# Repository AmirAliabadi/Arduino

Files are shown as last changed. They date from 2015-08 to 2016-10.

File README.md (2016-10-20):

# Arduino
Arduino related projects and libraries. 

quadcopter, dmp 6050, PID tuning

frame + esc + motor = 900g
each esc+motor+prop = 100g
large battery = 410g
small battery = 175g
flight controller = 50g

AUW with the wooden frame:
~1400g with large battery
~1200g with small battery

PID values that worked on the single boom:
Stable: 3.075, 0.0, 0.0
Rate: 0.475, 0.0, 0.004
Alpha: 0.92

Stable: 3.11, 0.0, 0.00
Rate: 0.515, 0.0, 0.08
Alpha: 0.80

-----
For the threaded brushless motors:
The direction you want the motor to spin is the direction that causes the nut to get tighter if you hold the nut still with your fingers.

ESC motor pairs
attach sync noise not in sync
001 paired with 001
xxx paired with 002

attach sync noise in sync 
001 paired with 003
xxx paired with 002

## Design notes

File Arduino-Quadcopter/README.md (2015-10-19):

Arduino-Quadcopter
=========

An arduino sketch for controlling a quadcopter. Uses RC and the MPU-6050 chip.

This is a simple arduino sketch that allows you to take over control over a quadcopter with the arduino board.
Because I've made this sketch primarily for private use, the sketch relies on certain hardware, but should also be
usable with different hardware with a bit of customization work.

This sketch was only tested on the Arduino Uno rev 3 board, so it might not work on other arduino-like boards without
making changes.

The arducopter sketch needs three things to work at the moment:

- A RC receiver with a minimum of 4 channels
- The MPU-6050 gyro/accelerometer chip
- Four ESCs with a known minimum and maximum value

At the moment, the sketch doesn't implement all features as I can only update it as fast as I can run new tests
with my quadcopter.
Complete features are:

- Arming of ESCs with given min/max values
- Control over pitch, roll and yaw through motor speed balances
- Control over pitch, roll and yaw through RC
- Controll over vertical speed through RC
- Calculation of current pitch, roll and yaw via the DMP unit on the MPU-6050

Planned features are:

- Automatic stabilisation of flight via MPU-6050 (complete but not fine tuned)
- Assisted safe landing through free fall detection

More features will be added as I expand the usage of my quadcopter.

In order to use this sketch, you will need to install the libraries from [arducopter/libraries](https://github.com/strangedev/arducopter/tree/master/libraries)
on your computer.

Note:
You cannot use the original Arduino-PID-Library wih this sketch. Please use the modified one included in this repo.

I want to thank [Jeff Rowberg](https://github.com/jrowberg), who created the great library [i2cdevlib](https://github.com/jrowberg/i2cdevlib) for using all
kinds of I2C devices including the MPU-6050 with the arduino board.
I also want to thank [br3ttb](https://github.com/br3ttb), who created the [Arduino-PID-Libary](https://github.com/br3ttb/Arduino-PID-Library/) which helped me save a lot of time.
Without their contributions to the open source community I couldn't have done this project.

Modifying the sketch
====================
***
*Note:* If you have questions about the code or the compatability of the code and certain hardware, you've spotted a bug or need help with your project, please open a new github issue rather than sending me an e-mail. That way, I don't have to answer questions twice and you'll get quicker answers. Thank you.
***
As I mentioned earlier, the sketch relies on certain hardware, but should work with all similar hardware aswell.
Fundemtal paramters of the used hardware, like the pin it's connected to, or minimum/maximum values of the ESCs are ``#define``'d
at the top of the sketch and can easily be changed to whatever value you prefer.

You might also want to change how the motor speed is affected by the signal coming in from the RC, for exmaple if your
copter is lighter or heavier than mine. At the moment this can only be done by changing the used equations in
``calculateVelocities()``.
However, I will improve my algorithms in the future and will probably find a way to easily fine tune the paramters of
the motor control.

Note:

The MPU-6050 board currently is the only supported gyro/accelerometer hardware and can only be connected in one specific 
way, due to the requirements of I2C and the fixed position of the Arduino's external interrupt pin.

License
=======

This project is licensed under the MIT license (see the included license file for more information).

Note: The libraries used in this project might not be licensed under the MIT license. I've made sure that the usage of all libraries as a part of this project, my modifications and the redistribution of the modified and unmodified libraries are permitted by the respective licenses, but the permissions of the MIT license might not apply, especially in regard to relicensing.

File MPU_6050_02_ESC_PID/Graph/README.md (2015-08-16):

#### Developed by Kristian Lauszus, TKJ Electronics 2012

The code is released under the GNU General Public License.
_________

This is the [Processing](http://processing.org/) application I made to visualize the data sent from the Arduino.

This should be used with the [MPU-6050](../) code I have provided.

Note that you properly need to change the serial port for it to work.

The serial port can be changed at the following line in the code:

```
serial = new Serial(this, Serial.list()[0], 115200);
```

For more information fell free to post a question at the guide: <http://arduino.cc/forum/index.php/topic,58048.0.html> or send me an email at <kristianl@tkjelectronics.dk>.

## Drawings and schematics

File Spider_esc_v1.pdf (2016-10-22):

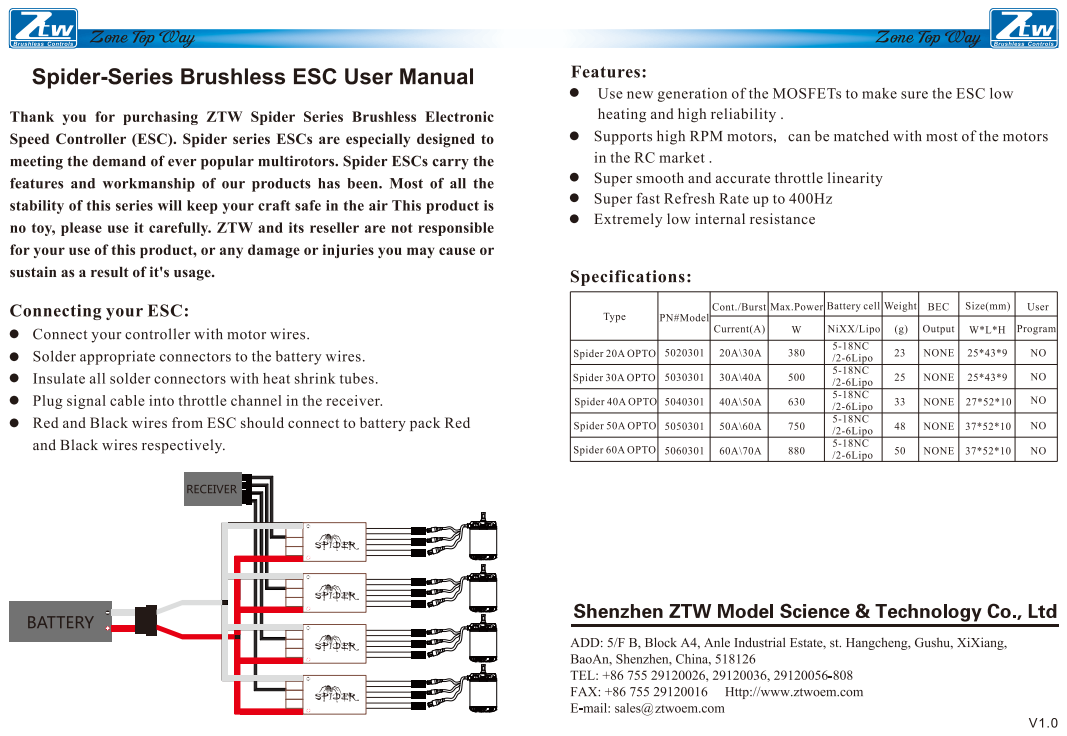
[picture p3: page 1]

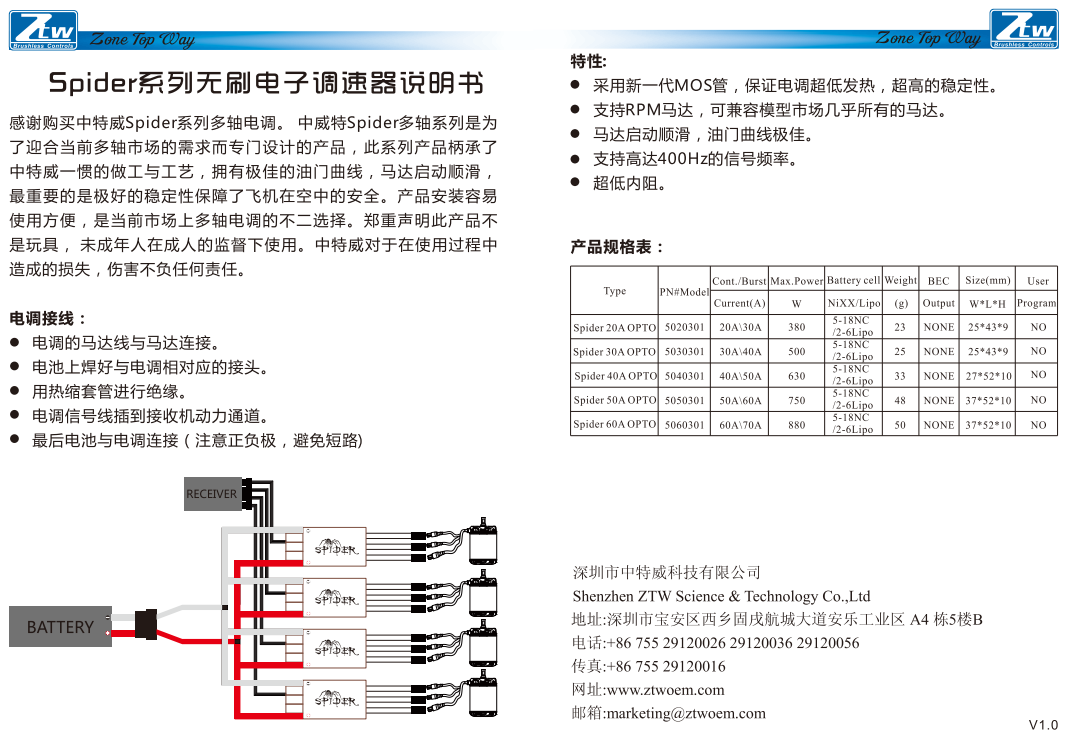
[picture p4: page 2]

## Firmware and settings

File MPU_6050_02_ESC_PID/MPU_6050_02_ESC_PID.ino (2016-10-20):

#include "Config.h"

//#include "MyServo.h"
//#define _ESC_ MyServo

#include "ESC.h"
#define _ESC_ ESC


#include <PID_v1.h>
#if I2CDEV_IMPLEMENTATION == I2CDEV_ARDUINO_WIRE
#include "Wire.h"
#endif
#include "I2Cdev.h"
#include "MPU6050_6Axis_MotionApps20.h"
//#include "MPU6050_9Axis_MotionApps41.h"
//#include "MPU6050.h" // not necessary if using MotionApps include file

byte update_pid_settings_needed = 1;
byte selected_pot_tuning = 0;
byte aserial_data_mode = 0;

float alpha = 0.88;
int pid_refresh_rate = 10;

#define DEBUG
//#define USE_INTERRUPTS
#define CASCADE_PIDS

/*
 * Single Boom PID values
 * ----------------------
 * 5.07, 0.00, 0.00
 * 0.443, 0.034, 0.112
 * 
 * 2.49, 0.00, 0.00       works but slugish
 * 0.376, 0.004, 0.004
 * 
 * alpha 0.02, pid rate 20
 * 2.615, 0.085, 0.065
 * 0.41, 0, 0.004
 * 
 * found some checkin notes about the d-term causing chatter
 *                           4.70,  0.0, 0.00,    // Stable P/I/D // .89,0,.23
 *                           1.20,  0.0, 0.16,    // Rate P/I/D
 *                           
 *  3.135, 0.0, 0.0
 *  0.672, 0.01, 0.013
 *  alpha 0.2, PID Refresh 5.0
 * 
 * *
 * Single Boom Quad PID
 * ---------------------
 * 6.885  0.00  0.405
 * 0.551  0.00  0.184
 * 
 * * 2.865 0.00 0.00
 * * 0.429 0.005 0.038
 */

///////////////////////////////////`
// user inputs
float input_values[17] = { 0,                       // thrust
                           3.135, 0.000, 0.000,     // Stable Pitch/Role PID P/I/D // .89, 0, .23
                           0.672, 0.010, 0.013,     // Rate Pitch/Role PID P/I/D
                           2.000, 0.000, 0.000,     // Stable Yaw 1.0, 0, 0.2,                 // YAW P/I/D
                           0.110, 0.000, 0.000,     // Stable Yaw 1.0, 0, 0.2,                 // YAW P/I/D
                           0.0, // setpoint yaw
                           0.0, // setpoint roll
                           0.0, // setpoint pitch
                           12.6                     // battery voltage level
                           };

// PID values:
// 4.7 / 0 / 0 | 1.2 / 0 / 0.16
// 2.681 / 0 / 0 | 0.967 / 0.125 / 0.096                           

#define INPUT_THRUST          input_values[0]

#define INPUT_STB_PID_P       input_values[1]
#define INPUT_STB_PID_I       input_values[2]
#define INPUT_STB_PID_D       input_values[3]

#define INPUT_RAT_PID_P       input_values[4]
#define INPUT_RAT_PID_I       input_values[5]
#define INPUT_RAT_PID_D       input_values[6]

#define INPUT_YAW_PID_P       input_values[7]
#define INPUT_YAW_PID_I       input_values[8]
#define INPUT_YAW_PID_D       input_values[9]

#define INPUT_YAW_RATE_PID_P       input_values[10]
#define INPUT_YAW_RATE_PID_I       input_values[11]
#define INPUT_YAW_RATE_PID_D       input_values[12]

#define INPUT_SETPOINT_YAW    input_values[13]
#define INPUT_SETPOINT_ROLL   input_values[14]
#define INPUT_SETPOINT_PITCH  input_values[15]
#define INPUT_VOLTAGE_LEVEL   input_values[16]

uint8_t setpoint_changed = SETPOINT_UNCHANGED;


float setpoint[3] = {0, 0, 0};
float last_setpoint[3] = {0, 0, 0};

//
//////////////////////////////////////////////////////////////////

//////////////////////////////////////////////////////////////////
// function pointer to what should be happing in the loop()
void (*process)(void);
void (*send_serial)(byte mode);
//
//////////////////////////////////////////////////////////////////

////////////////////////////////////////////////////////////////
// MPU setup
MPU6050 mpu;

// MPU control/status vars
bool dmpReady = false;  // set true if DMP init was successful
uint8_t mpuIntStatus;   // holds actual interrupt status byte from MPU
uint8_t devStatus;      // return status after each device operation (0 = success, !0 = error)
uint16_t packetSize;    // expected DMP packet size (default is 42 bytes)
uint16_t fifoCount;     // count of all bytes currently in FIFO
uint8_t fifoBuffer[64]; // FIFO storage buffer


// orientation/motion vars
Quaternion q;           			// [w, x, y, z]         quaternion container
VectorInt16 aa;         			// [x, y, z]            accel sensor measurements
VectorInt16 aaReal;     			// [x, y, z]            gravity-free accel sensor measurements
VectorInt16 aaWorld;    			// [x, y, z]            world-frame accel sensor measurements
VectorFloat gravity;    			// [x, y, z]            gravity vector

#ifdef CASCADE_PIDS    
VectorInt16 gyro;
VectorInt16 gyro1;
#endif

float ypr[3]      = {0.0f, 0.0f, 0.0f};
float ypr_last[3] = {0.0f, 0.0f, 0.0f};
float yw_offset   = 0.0;
float ac_offset   = 0.0;
float bd_offset   = 0.0;
//
////////////////////////////////////////////////////////////////


////////////////////////////////////////////////////////////////
// ESC
_ESC_ esc_a;
_ESC_ esc_b;
_ESC_ esc_c;
_ESC_ esc_d;

uint16_t va = MIN_ESC_SIGNAL;
uint16_t vb = MIN_ESC_SIGNAL;
uint16_t vc = MIN_ESC_SIGNAL;
uint16_t vd = MIN_ESC_SIGNAL;

uint16_t v_ac = 0;
uint16_t v_bd = 0;
//
////////////////////////////////////////////////////////////////

////////////////////////////////////////////////////////////////
// PID settings
float input_ypr[3]    = {0.0f, 0.0f, 0.0f};
float output_ypr[3]   = {0.0f, 0.0f, 0.0f};
float input_gyro[3]   = {0.0f, 0.0f, 0.0f};
float output_rate[3]  = {0.0f, 0.0f, 0.0f};

// input / output /setpoint
PID pid_stable[3]  = {
  PID(&input_ypr[YW], &output_ypr[YW], &setpoint[YW], 0, 0, 0, DIRECT),
  PID(&input_ypr[BD], &output_ypr[BD], &setpoint[BD], 0, 0, 0, DIRECT), 
  PID(&input_ypr[AC], &output_ypr[AC], &setpoint[AC], 0, 0, 0, DIRECT)
};

#ifdef CASCADE_PIDS
PID pid_rate[3] = {
  PID(&input_gyro[YW], &output_rate[YW], &output_ypr[YW], 0, 0, 0, DIRECT),
  PID(&input_gyro[BD], &output_rate[BD], &output_ypr[BD], 0, 0, 0, DIRECT),
  PID(&input_gyro[AC], &output_rate[AC], &output_ypr[AC], 0, 0, 0, DIRECT)
};
#endif

//
////////////////////////////////////////////////////////////////

////////////////////////////////////////////////////////////////
// MISC items
uint16_t system_check = INIT_CLEARED;

#ifdef DEBUG
long log_line = 0;
long last_log = 0;
#endif
long last_blink = 0;

////////////////////////////////////////////////////////////////


//// ================================================================
//// ===               INTERRUPT DETECTION ROUTINE                ===
//// ================================================================
//
#ifdef USE_INTERRUPTS
volatile bool mpuInterrupt = false;     // indicates whether MPU interrupt pin has gone high
void dmpDataReady()
{
  mpuInterrupt = true;

//  read_mpu();
//  read_throttle();
//  read_setpoint();
//  read_battery_voltage();
//  update_pid_settings();
//  
//  process();  
}
#endif

//////////////////////////////////////////////////////////////////////
// setup
void setup()
{
#ifdef DEBUG
  Serial.begin(115200); 
  while (!Serial);
#endif

  // configure LED for output
  pinMode(LED_PIN, OUTPUT);
  
  disarm_esc();
  init_i2c();
  init_pid();
  init_mpu();

  process = &wait_for_stable_process; //check_if_stable_process; //arm_esc_process;

  send_serial = &SerialSend_A;
}
//////////////////////////////////////////////////////////////////////


// ================================================================
// ===                    MAIN PROGRAM LOOP                     ===
// ================================================================
void loop()
{
  if ( millis() - last_blink > (system_check & INIT_ESC_ARMED == INIT_ESC_ARMED ? (INPUT_THRUST == 0 ? BLINK_FREQUENCY : BLINK_FREQUENCY / 2) : BLINK_FREQUENCY / 16) )
  {
    last_blink = millis();

    digitalWrite(LED_PIN, !digitalRead(LED_PIN));
  }

  if (!dmpReady) return;

#ifdef USE_INTERRUPTS
  // wait for MPU interrupt or extra packet(s) available
  while (!mpuInterrupt) // && fifoCount < packetSize)
  {
    read_throttle();        if (mpuInterrupt) break;
    read_setpoint();        if (mpuInterrupt) break;
    read_battery_voltage(); if (mpuInterrupt) break;
    update_pid_settings();  if (mpuInterrupt) break;

    process();
  }  
#endif

  read_mpu();
  read_throttle();
  read_setpoint();
  read_battery_voltage();
  update_pid_settings();
  
  process();

}

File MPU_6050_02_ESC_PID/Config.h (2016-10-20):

#define LED_PIN 13            // (Arduino is 13, Teensy is 11, Teensy++ is 6)
#define LOG_FREQUENCY  50     // ms DEBUG Logging interval
#define BLINK_FREQUENCY 1000

#define INIT_CLEARED          0b00000000
#define INIT_ESC_ATTACHED     0b00000001
#define INIT_ESC_ARMED        0b00000010
#define INIT_THROTTLE_ACTIVE  0b00000100
#define INIT_MOTORS_ENABLED   0b00001000
#define INIT_MPU_ARMED        0b00010000
#define INIT_MPU_STABLE       0b00100000
#define INIT_PID_ON           0b01000000
#define INIT_THROTTLE_ZEROED  0b10000000


#define SETPOINT_UNCHANGED    0b000
#define SETPOINT_CHANGED_AC   0b001
#define SETPOINT_CHANGED_BD   0b010
#define SETPOINT_CHANGED_YW   0b100

#define MPU_3

#ifdef MPU_1
#define MPU6050_ACCEL_OFFSET_X 699
#define MPU6050_ACCEL_OFFSET_Y -669
#define MPU6050_ACCEL_OFFSET_Z 1301
#define MPU6050_GYRO_OFFSET_X  47
#define MPU6050_GYRO_OFFSET_Y  -16
#define MPU6050_GYRO_OFFSET_Z  -30
#endif

#ifdef MPU_2
#define MPU6050_ACCEL_OFFSET_X -6542
#define MPU6050_ACCEL_OFFSET_Y -1314
#define MPU6050_ACCEL_OFFSET_Z 840
#define MPU6050_GYRO_OFFSET_X  39
#define MPU6050_GYRO_OFFSET_Y  -49
#define MPU6050_GYRO_OFFSET_Z  15
#endif

#ifdef MPU_3
#define MPU6050_ACCEL_OFFSET_X -62
#define MPU6050_ACCEL_OFFSET_Y 366
#define MPU6050_ACCEL_OFFSET_Z 1416
#define MPU6050_GYRO_OFFSET_X  161
#define MPU6050_GYRO_OFFSET_Y  145
#define MPU6050_GYRO_OFFSET_Z  -19
#endif


// mpu1
// 699  -669  1301  47  -16 -30
// 757  -662  1301  47  -12 -30

// mpu2
// -6640  -1344  832   38    -52   16
// -6542  -1314  840   39    -49   15
// -6545  -1318  834   45    -48   14

// mpu3
// 46 365 1393  163 143 -19
// 47 364 1394  162 143 -20
// 40 376 1398  162 142 -19
// 41 377 1398  162 142 -19
/*
Sensor readings with offsets:  -3  -7  16380 0 0 1
Your offsets: -64 373 1417  161 145 -19

Sensor readings with offsets:  2 -1  16388 0 1 1
Your offsets: -62 366 1416  161 145 -19
*/


/*
 *             (y)
                A Pitch +
                |
        Roll -  |
     (x)D -----[Y]----- B Roll +
                |(z)
                !
                C Pitch -

                USBaz
*/
#define YW 0
#define YAW 0
#define BD 1
#define ROLL 1
#define AC 2
#define PITCH 2
////////////////////////////////////////////////////////////////

////////////////////////////////////////////////////////////////
// throttle
#define THROTTLE_PIN 0

////////////////////////////////////////////////////////////////
// PID Tunning with a POT
#define Kp_PIN 0
#define Ki_PIN 1
#define Kd_PIN 2

////////////////////////////////////////////////////////////////
// ESC Settings
#define ESC_ARM_DELAY     3000
#define MAX_ESC_SIGNAL    2000    // This is the max output that will be sent to ESC.
#define MIN_ESC_SIGNAL    1000    // Minimum ESC signal
#define MIN_ESC_CUTOFF    1200    // Minimum ESC signal to ARM less than or equal to this should turn off motor completely
#define MOTOR_PIN_A       3       // setup with 500hz PWM pins
#define MOTOR_PIN_B       9       
#define MOTOR_PIN_C       11       
#define MOTOR_PIN_D       10      
/*
 * pin pairs:
 * 3 - 11 : default PWM frequency: 490.20 Hz
 * 9 - 10 : default PWM frequency: 490.20 Hz
 * 5 - 6  : default PWM frequency: 976.56 Hz
 */

/*
 * 
If you use the default values set by the Arduino Diecimila's bootloader, these are your PWM frequencies:
Arduino Pins 5 and 6: 1kHz
Arduino Pins 9, 10, 11, and 3: 500Hz
 */

// THROTTLE SETTINGS
#define MAX_INPUT_THRUST  1000    // 
#define MIN_INPUT_THRUST  0       // 

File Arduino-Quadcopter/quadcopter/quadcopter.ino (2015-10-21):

#ifndef QUADARDU
#define QUADARDU

#include <Servo.h>
#include <Wire.h>
#include <I2Cdev.h>
#include <helper_3dmath.h>
#include <MPU6050_6Axis_MotionApps20.h>
#include <PID_v1.h>
#include <PinChangeInt.h>
#include <PinChangeIntConfig.h>

#define DEBUG
#define MPU6050_ACCEL_OFFSET_X -6640
#define MPU6050_ACCEL_OFFSET_Y -1344
#define MPU6050_ACCEL_OFFSET_Z 832
#define MPU6050_GYRO_OFFSET_X  38
#define MPU6050_GYRO_OFFSET_Y  -52
#define MPU6050_GYRO_OFFSET_Z  -16

// board1 :   722  -654   1305  48    -16   -32
// board2 : -6640  -1344  832   38    -52   16



/*  Arduino Pin configuration
 *
 */

#define ESC_A 9
#define ESC_B 5
#define ESC_C 6
#define ESC_D 10

#define RC_1 13
#define RC_2 12
#define RC_3 11
#define RC_4 10
#define RC_5 8
#define RC_PWR A0


/* ESC configuration
 *
 */

#define ESC_MIN 1100 //22
#define ESC_MAX 1800 //115
#define ESC_TAKEOFF_OFFSET 1140 //30
#define ESC_ARM_DELAY 5000

/* RC configuration
 *
 */

#define RC_HIGH_CH1 1000
#define RC_LOW_CH1 2000
#define RC_HIGH_CH2 1000
#define RC_LOW_CH2 2000
#define RC_HIGH_CH3 1000
#define RC_LOW_CH3 2000
#define RC_HIGH_CH4 1000
#define RC_LOW_CH4 2000
#define RC_HIGH_CH5 1000
#define RC_LOW_CH5 2000
#define RC_ROUNDING_BASE 50

/*  PID configuration
 *
 */

#define PITCH_P_VAL .01
#define PITCH_I_VAL 0
#define PITCH_D_VAL .001

#define ROLL_P_VAL .01
#define ROLL_I_VAL 0 //5
#define ROLL_D_VAL .001

#define YAW_P_VAL 0
#define YAW_I_VAL 0 //5
#define YAW_D_VAL 0


/* Flight parameters
 *
 */

#define PITCH_MIN -30
#define PITCH_MAX 30
#define ROLL_MIN -30
#define ROLL_MAX 30
#define YAW_MIN -180
#define YAW_MAX 180
#define PID_PITCH_INFLUENCE 20
#define PID_ROLL_INFLUENCE 20
#define PID_YAW_INFLUENCE 20


/*  MPU variables
 *
 */

MPU6050 mpu;                           // mpu interface object


uint8_t mpuIntStatus;                  // mpu statusbyte
uint8_t devStatus;                     // device status
uint16_t packetSize;                   // estimated packet size
uint16_t fifoCount;                    // fifo buffer size
uint8_t fifoBuffer[64];                // fifo buffer

Quaternion q;                          // quaternion for mpu output
VectorFloat gravity;                   // gravity vector for ypr
float yrp[3] = {0.0f, 0.0f, 0.0f};     // yaw pitch roll values
float yrpLast[3] = {0.0f, 0.0f, 0.0f};

volatile bool mpuInterrupt = false;    //interrupt flag

/* Interrupt lock
 *
 */

boolean interruptLock = false;

/*  RC variables
 *
 */

float ch1, ch2, ch3, ch4, ch5;         // RC channel inputs

unsigned long rcLastChange1 = micros();
unsigned long rcLastChange2 = micros();
unsigned long rcLastChange3 = micros();
unsigned long rcLastChange4 = micros();
unsigned long rcLastChange5 = micros();

/*  Motor controll variables
 *
 */

int velocity;                          // global velocity

float bal_ac, bal_bd;                 // motor balances can vary between -100 & 100
float bal_axes;                       // throttle balance between axes -100:ac , +100:bd

int va, vb, vc, vd;                    //velocities
int v_ac, v_bd;                        // velocity of axes

Servo a, b, c, d;

/*  PID variables
 *
 */

#define YAW  0
#define PITCH 2
#define ROLL 1

PID pitchReg(&yrp[PITCH], &bal_ac, &ch2, PITCH_P_VAL, PITCH_I_VAL, PITCH_D_VAL, REVERSE);
PID rollReg(&yrp[ROLL], &bal_bd, &ch1, ROLL_P_VAL, ROLL_I_VAL, ROLL_D_VAL, REVERSE);
PID yawReg(&yrp[YAW], &bal_axes, &ch4, YAW_P_VAL, YAW_I_VAL, YAW_D_VAL, DIRECT);


/*  Filter variables
 *
 */

float ch1Last, ch2Last, ch4Last, velocityLast;

/*  Setup function
 *
 */

long last_log = 0;

float yaw_offset, pitch_offset, roll_offset;

void setup() {
    a.detach();
    c.detach();
    b.detach();
    d.detach();

    delay(10);
  
#ifdef DEBUG                        // Device tests go here
  Serial.begin(115200);                 // Serial only necessary if in DEBUG mode
  Serial.flush();
#endif

  //initRC();                            // Self explaining
  initMPU();
  initESCs();
  initBalancing();
  initRegulators();

  /*
    for(int i=0; i < 500; i++ ) {
      getYPR();
      delay(5);
    }

    yaw_offset = yrp[0];
    pitch_offset = yrp[2];
    roll_offset = yrp[1]; */


}

/* loop function
 *
 */

 boolean is_stable = 0;
 float last_yaw = 333;

void loop() {

  while (!mpuInterrupt) { // && fifoCount < packetSize){

    /* Do nothing while MPU is not working
     * This should be a VERY short period
     */

  }

  getYPR();

  if( is_stable ) {
    computePID();
    calculateVelocities();
    updateMotors();
  } else {
    if (millis() - last_log > 2000)
    {
      Serial.print(yrp[0]); Serial.print(F("\t"));
      Serial.println(last_yaw);
      last_log = millis();
      if( yrp[0] == last_yaw )
      {
        is_stable = 1;
        yaw_offset = yrp[0];
      } 
      else 
      {
        last_yaw = yrp[0];
      }
    }
  }
}

/*  computePID function
 *
 *  formats data for use with PIDLib
 *  and computes PID output
 */

void computePID() {

  acquireLock();

  /*
  ch1 = floor(ch1/RC_ROUNDING_BASE)*RC_ROUNDING_BASE;
  ch2 = floor(ch2/RC_ROUNDING_BASE)*RC_ROUNDING_BASE;
  ch4 = floor(ch4/RC_ROUNDING_BASE)*RC_ROUNDING_BASE;

  ch2 = map(ch2, RC_LOW_CH2, RC_HIGH_CH2, PITCH_MIN, PITCH_MAX);
  ch1 = map(ch1, RC_LOW_CH1, RC_HIGH_CH1, ROLL_MIN, ROLL_MAX);
  ch4 = map(ch4, RC_LOW_CH4, RC_HIGH_CH4, YAW_MIN, YAW_MAX);

  if((ch2 < PITCH_MIN) || (ch2 > PITCH_MAX)) ch2 = ch2Last;
  if((ch1 < ROLL_MIN) || (ch1 > ROLL_MAX)) ch1 = ch1Last;
  if((ch4 < YAW_MIN) || (ch4 > YAW_MAX)) ch4 = ch4Last;

  ch1Last = ch1;
  ch2Last = ch2;
  ch4Last = ch4;
  */
  ch1Last = 0;
  ch2Last = 0;
  ch4Last = 0;

////
//
////

  pitchReg.Compute();
  rollReg.Compute();
  yawReg.Compute();

  releaseLock();

}

/*  getYPR function
 *
 *  gets data from MPU and
 *  computes pitch, roll, yaw on the MPU's DMP
 */

void getYPR() {

  mpuInterrupt = false;
  mpuIntStatus = mpu.getIntStatus();
  fifoCount = mpu.getFIFOCount();

  if ((mpuIntStatus & 0x10) || fifoCount >= 1024) {

    Serial.println(F("Fifo overflow!"));
    mpu.resetFIFO();

  } else if (mpuIntStatus & 0x02) {

    while (fifoCount < packetSize) fifoCount = mpu.getFIFOCount();

    mpu.getFIFOBytes(fifoBuffer, packetSize);

    fifoCount -= packetSize;

    mpu.dmpGetQuaternion(&q, fifoBuffer);
    mpu.dmpGetGravity(&gravity, &q);
    mpu.dmpGetYawPitchRoll(yrp, &q, &gravity);

    /////
    //
    yrp[0] = yrp[0] * 180 / M_PI;
    yrp[1] = yrp[1] * 180 / M_PI;
    yrp[2] = yrp[2] * 180 / M_PI;
    
    yrp[0] = (float)((int)(( (yrp[0] - yaw_offset) * 10.0) +.5))/10.0;
    yrp[1] = (float)((int)((yrp[1] * 10.0) +.5))/10.0;
    yrp[2] = (float)((int)((yrp[2] * 10.0) +.5))/10.0;    
    
    if (abs(yrp[0] - yrpLast[0]) > 30) yrp[0] = yrpLast[0];
    if (abs(yrp[1] - yrpLast[1]) > 30) yrp[1] = yrpLast[1];
    if (abs(yrp[2] - yrpLast[2]) > 30) yrp[2] = yrpLast[2];
    
    yrpLast[0] = yrp[0];
    yrpLast[1] = yrp[1];
    yrpLast[2] = yrp[2];
    //
    //////    

  }

}
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

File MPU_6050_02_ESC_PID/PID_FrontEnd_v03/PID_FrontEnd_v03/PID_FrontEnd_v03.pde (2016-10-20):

/********************************************************
 * Arduino PID Tuning Front-End,  Version 0.3
 * by Brett Beauregard
 * License: Creative-Commons Attribution Share-Alike
 * April 2011
 *
 * This application is designed to interface with an
 * arduino running the PID Library.  From this Control
 * Panel you can observe & adjust PID performance in 
 * real time
 *a
 * The ControlP5 library is required to run this sketch.
 * files and install instructions can be found at
 * http://www.sojamo.de/libraries/controlP5/
 * 
 ********************************************************/

import java.nio.ByteBuffer;
import processing.serial.*;
import controlP5.*;

float last_throttle_position = 0;

float kp=0,ki=0,kd=0,krp=0,kri=0,krd=0;
float cur_throttle ;
float alpha =0.0 ;
float pid_refresh_rate=10.0 ;

/***********************************************
 * User spcification section
 **********************************************/
int windowWidth = 1350;      // set the size of the 
int windowHeight = 690;     // form

float InScaleMin = -75;       // set the Y-Axis Min
float InScaleMax = 75;    // and Max for both
float OutScaleMin = -125;      // the top and 
float OutScaleMax = 125;    // bottom trends


int windowSpan = 2000;//0;//00;    // number of mS into the past you want to display
int refreshRate = 10;      // how often you want the graph to be reDrawn;

float displayFactor = 1; //display Time as Milliseconds
//float displayFactor = 1000; //display Time as Seconds
//float displayFactor = 60000; //display Time as Minutes

// if you'd like to output data to 
// a file, specify the path here
String outputFileName = ""; 

/***********************************************
 * end user spec
 **********************************************/

int nextRefresh;
int arrayLength = windowSpan / refreshRate+1;
int[][] InputData = new int[3][arrayLength];
int[][] OutputData = new int[5][arrayLength];

float inputTop = 25;
float inputHeight = (windowHeight-70)*2/3;
float outputTop = inputHeight+50;
float outputHeight = (windowHeight-70)*1/3;

float ioLeft = 210, ioWidth = windowWidth-ioLeft-50;
float ioRight = ioLeft+ioWidth;
float pointWidth= (ioWidth)/float(arrayLength-1);

int vertCount = 10;
int nPoints = 0;

boolean madeContact =false;
boolean justSent = true;

Serial myPort;

ControlP5 controlP5;
controlP5.Button DRButton, DRrButton;

RadioButton serial_data_mode; //, tuning_mode;

float Input_Thrust, Input_Setpoint, Input_gyro, Input_angle, Output_angle, Output_gyro ;
byte i_serial_data_mode; 
float va,vb,vc,vd;
float pterm_stable, iterm_stable, dterm_stable;
float pterm_rate, iterm_rate, dterm_rate;

controlP5.Textlabel InputThrustLabel, InputSetpointLabel, InputGyroLabel, InputAngleLabel, AngleOutLabel, GyroOutLabel, AlphaLable, PidRefreshIntervalLabel;
controlP5.Textlabel PTermRateLabel, ITermRateLabel, DTermRateLabel;
controlP5.Textlabel PLabel, ILabel, DLabel, DRLabel, DRCurrent, DRrLabel, DRrCurrent, PrLabel, IrLabel, DrLabel ;

controlP5.Textlabel SPField; 

controlP5.Slider throttle_slider;

PrintWriter output;
PFont AxisFont, TitleFont; 

void setup()
{
  int group_x =0;
  int group_y =0;
  
  frameRate(30); // 30
  size(1350 , 690);

  println(Serial.list());   // * Initialize Serial
  
  if( Serial.list().length > 0 ) {
    myPort = new Serial(this, Serial.list()[0], 115200);                //   Communication with
    myPort.bufferUntil(10);         //   the Arduino
  }
  
  controlP5 = new ControlP5(this);                                    // * Initialize the various
  
  group_x = 80; group_y=140;
  
  controlP5.addTextlabel("t-1","Setpoint",group_x-80,group_y);  
  SPField= controlP5.addTextlabel("Setpoint","", group_x, group_y);
  
  controlP5.addTextlabel("t1","Throttle",group_x-80,group_y+=15);
  InputThrustLabel=controlP5.addTextlabel("InputThrustLabel","", group_x, group_y);
  
  controlP5.addTextlabel("t2","Setpoint",group_x-80,group_y+=15);
  InputSetpointLabel=controlP5.addTextlabel("InputSetpointLabel","",group_x,group_y);

  controlP5.addTextlabel("t4","Input Angle",group_x-80,group_y+=15);
  InputAngleLabel=controlP5.addTextlabel("InputAngleLabel","",group_x,group_y); 
  controlP5.addTextlabel("t3","Input Gyro",group_x-80,group_y+=15);
  InputGyroLabel=controlP5.addTextlabel("InputGyroLabel","",group_x,group_y);

  controlP5.addTextlabel("t5","Out Angle",group_x-80,group_y+=15);
  AngleOutLabel=controlP5.addTextlabel("AngleOutLabel","",group_x,group_y); 
  controlP5.addTextlabel("t6","Out Gyro",group_x-80,group_y+=15);
  GyroOutLabel=controlP5.addTextlabel("GyroOutLabel","",group_x,group_y);

  controlP5.addTextlabel("t7","Alpha",group_x-80,group_y+=15);
  AlphaLable=controlP5.addTextlabel("AlphaLable","",group_x,group_y);

  controlP5.addTextlabel("t71","PID Refresh",group_x-80,group_y+=15);
  PidRefreshIntervalLabel=controlP5.addTextlabel("PidRefreshIntervalLabel","",group_x,group_y);
  
  controlP5.addTextlabel("t72","PTerm Rate",group_x-80,group_y+=15);
  PTermRateLabel=controlP5.addTextlabel("PTermRateLabel","10",group_x,group_y);
  controlP5.addTextlabel("t73","ITerm Rate",group_x-80,group_y+=15);
  ITermRateLabel=controlP5.addTextlabel("ITermRateLabel","10",group_x,group_y);
  controlP5.addTextlabel("t74","DTerm Rate",group_x-80,group_y+=15);
  DTermRateLabel=controlP5.addTextlabel("DTermRateLabel","10",group_x,group_y);
  
  controlP5.addTextlabel("t8","Stable",group_x-80,group_y+=35);  
  controlP5.addTextlabel("t81","Rate",group_x,group_y);    
  
  controlP5.addTextlabel("t9","P: ",group_x-80,group_y+=15);    
  PLabel=controlP5.addTextlabel("Ps","0.00",group_x-70,group_y);                    //
  PrLabel=controlP5.addTextlabel("Pr","0.00",group_x,group_y);                    //
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

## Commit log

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2015-08-19 updated handle noise from the 6050 and updated to log the PID terms that are in effect. The serial out can easily be graphed in google charts.
    [MPU_6050_02_ESC_PID.ino]
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2015-09-07 more updates related to tuning pid, updated to use serialEvent() to read inputs from serial.
2015-09-11 more updates, working on eliminating vibrations from motors.
    [Logging.ino, MPU_6050_02_ESC_PID.ino]
2015-09-14 more PID tuning. A found out why MPU reading were bogus after a certain period of time.
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2015-09-17 finally good PID tuning values. The trick was to increate the PID compute frequency. The defualt of once every 100ms the PID_v1 has was to slow.
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2015-09-18 more PID tuning. I have found some PID values that seem to work.
2015-09-19 tested out the spyder ESC and they didn't perform as well as the yellow no-name amazone ESC i have been used. need to look into it more. Also, experimenting with reseting the PID when the setpiont ch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
    [Config.h, ESC.ino, ESC_Arming_with_POT.ino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]
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2015-09-25 bug fixes related to switching to bitmasks. Added the adaptive pid tuning and the concept of PD controller when far from setpoint and PID controller when close to setpoint
    [Config.h, ESC.ino, Logging.ino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]
2015-09-26 added the yaw and have started to get ready for the second boom to be in place.
2015-09-27 still working out the pid tunings and the adaptive pid values. found out that the quad stand was binding make it appear as if things were more stable than they actually were.
    [ESC.ino, I2C.ino, Inputs.ino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]
2015-09-30 removed teh fifoCount < packetSize check and convert all serial prints to use the F() macro. This has fixed all banging issues and reduced to memory footprint. Enbaled the BD boom. Close to running t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
    [Config.h, ESC.ino, Inputs.ino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]
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2015-10-04 still trying to get the PID tunings just right. Finally got the PID values setting from the potentiometer.
2015-10-05 more pid tuning. I have the pots works nicely so PID tuning is much easier now.
2015-10-07 more pid tuning. I have settled on some pid value that I will use with teh full quadcopter out of the gate.
2015-10-12 fixed up reset behavior to insure motors are off after a reset event
    [ESC.ino, Inputs.ino, MPU.ino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]
2015-10-13 quad in plus mode, not hovering even though the single boom test rig was hovering nicelyt. could be inconsitent esc calibration, max_esc_input limits (for safety/testing, this might need to be remove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
2015-10-14 more updates related to PID tuning with the full quadcopter. added fritzing PCB
    [Quadcopter_6050.fzz]
2015-10-14 with the full quad setup, stability is no where in sight. could be the frame is out of balance, it want to drift in the same direction each time. could be ESC not calibrated the same (bought cheap ES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
    [Config.h, ESC_Arming_with_POT.ino, Inputs.ino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]
2015-10-15 updated PID tunings to be for the heavier quadcopter. Getting much closer to an initial, stable hover. need to get the YAW pid values tuned.
2015-10-15 Updated the fritzing PCB to incude LED and the BEC to the VCC in.
    [Quadcopter_6050.fzz]
2015-10-16 more PID tuning. quad drifts around and is trying but just won't hold. need to getting a good set of graphs going so I can see what is happening.
    [Inputs.ino, MPU_6050_02_ESC_PID.ino, PID.ino]
2015-10-16 upated fritzing, working on adding anlong input pins for PID tuning
    [Quadcopter_6050.fzz]
2015-10-16 minor updates
    [Quadcopter_6050.fzz]
2015-10-17 v1.0.0.1 of the PCB is done
    [Quadcopter_6050.fzz]
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2015-10-18 added another PID library. this one is from blue copter
    [Quadcopter_6050.fzz]
2015-10-18 including the PCB fab files
    [Quadcopter_6050_contour.gm1, Quadcopter_6050_copperBottom.gbl, Quadcopter_6050_copperTop.gtl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]
2015-10-18 back to using the serial to do pid tunings. switching to arduino uno with soldered on components.
2015-10-18 updated to match PWM pins used on soldered PCB board. Added started safety check with throttle. Updated the LPF on the IMU.
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2015-10-20 regrouping and starting over with the arduino-copter example. forked and updating slowing to match what I had originally done.
2015-10-21 MPU calibration done on the 2nd 6050. Still trying to figure out the PID tunings. Stable flight is no where in sight yet.
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2015-10-23 finished up the changes needed for the stable pid and the rate pid
2015-10-23 updates related to using a stablity PID and a rate PID. was not reading the gyro data correctly.
    [Config.h, Logging.ino, MPU.ino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]
2015-10-24 updated calibration settings for MPU #3 that is soldered to the Hip Cat v1.0.0.1 control board
2015-10-24 updated to actually use the rate pid output for the motor mix. Also added the calibartion settings for the 3rd mpu 6050.
2015-10-25 updated mpu calibration values for board #3, calibarte when mounted to the frame, and place frame on level ground.
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2015-10-25 fixed up the yaw pid to use the correct D value
    [PID.ino]
2015-10-25 filter out high frequency gryo changes. still no stable flight in sight.
2015-10-27 more fiddling around with the PID tunings. I don't see the light at the end of the tunnel yet.
2015-11-09 added low passfilter to gyro readings. this has helped. not sure where the LPF on the 6050 comes into play but I must be reading out the raw gyro values. Updated the sample code use to PID_v1 tuning 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
2015-11-10 more updated related to processing and serial communication to the arduino. The graphing is working great. The serial comm to arduino is just not great and very difficult to use. I will go back to us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
2015-11-11 the stable + rate PID loops are getting close to being tuned. observed the oscillation when D gain is to high. In the middle of fixing up the processing UI to work better with how I want to tune. I'm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
    [Inputs.ino, Logging.ino, MPU_6050_02_ESC_PID.ino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]
2015-11-11 fixed up a few things with the processing UI sketch
    [PID_FrontEnd_v03.pde]
2015-11-12 updated the processing UI to Arduino mode selection protocol. I can now use the pots in flight mode (throttle, setpoint), stable mode (stable PID tuning) and rate mode (Rate PID tuning).
2015-11-13 getting closer the PID tuning with a stable and rate PID loop. 2.681 / 0.967 - 0.125 - 0.096 looks good. Also found increating Stable P with some D works as well.
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2015-11-18 back to the full quad. Just won't go stable. did respond to setpoint change, almost to much of a respone, so maybe PID values are just not right yet
    [Logging.ino, PID_FrontEnd_v03.pde]
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2015-11-26 getting much closer now to stable flight, and might even say I have stable flight. The next issue is the wondering around it does and the lack of a compass to maintain a heading.
    [MPU_6050_02_ESC_PID.ino]
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2015-11-27 bug fixes related to the yaw pid tunings
    [Inputs.ino, PID.ino, PID_FrontEnd_v03.pde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]
2015-11-27 fixes related to YAW pid tuning
    [PID_FrontEnd_v03.pde, Process.ino]
2015-11-30 checking in debug data from processing app
    [20151129_run1.csv]
2015-11-30 adding MAVLink libraries. I have copied the v1.0 from the ardupilot code base and another v1.x (i think this is the same as v1.0) from the gcs website/github site.
    [20151129_run1.csv, 20151129_run1.xlsx]
2015-11-30 not working at this time. the throttle is getting cropped. I was trying to change to data types to be minium size possible to save space but something is now not working...
    [MPU_6050_02_ESC_PID.ino, PID_FrontEnd_v03.pde, Process.ino]
2015-12-01 updates to the processing UI so throttle can be controlled from UI
2015-12-02 more work on the processing UI and the serial protocol being used between processing and arduino.
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2015-12-06 more updates to processing UI related to key strokes for pid tuning and throttle.
2015-12-06 working out issues with serial comm between processing and arduino.
    [Logging.ino, MPU_6050_02_ESC_PID.ino, PID_FrontEnd_v03.pde]
2015-12-07 still hacking the serial protocol between processing and arduino. getting glitching comm.
    [Logging.ino, PID_FrontEnd_v03.pde]
2015-12-08 working out serial comm issues between processing and arduino
    [Logging.ino, PID_FrontEnd_v03.pde]
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2016-04-21 restarting project. Updated default pid tuning values to what seems to be working with a single boom.
2016-04-21 updated to latest i2cdev library. removed the interrupt pin from the 6050, don't need it
2016-04-24 Update how the byte array is being send and received over the serial port. working much better now. Started working on the min cutoff value for the throttle to avoid the props from flapping on/off at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
    [Config.h, Logging.ino, MPU.ino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]
2016-04-29 working on the throttle inputs and the motor mix. convinced the issue is with my motor mix algorithm.
    [Inputs.ino, Process.ino]
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2016-04-30 Added the yap pid tuning to processing and to the serial command to arduino
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2016-05-12 found that I had some limiters set on the PID. I have increased these limits to hopefully allow for more pid driven thrust differential.
2016-05-13 working better now with increased pid outputlimits. still a long way away but better....
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2016-05-17 updated the pids to be an array of pids to make it earier to do logging and debug prints. remove some minor things in the pid init routine and remove the reseting of the output_ypr when pid is set/re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
    [Logging.ino, MPU.ino, MPU_6050_02_ESC_PID.ino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]
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2016-05-18 updated the low pass filter to use an alpha of .2. removed more unneeded code, trying to make it more readable and hopefully spot any bugs.
    [Inputs.ino, MPU.ino, MPU_6050_02_ESC_PID.ino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]
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2016-05-20 PIDs are not working correctly anymore. Some minor code clean up, next up is track down what changed with the PIDs
    [PID.ino]
2016-05-21 more code clean up. pids seem to be setup correctly and working. Still trying to get the PID tuning to work...
    [ESC.ino, PID.ino, PID_FrontEnd_v03.pde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]
2016-05-22 updates to support changing PID direction. more code clean up. PID tuning not working yet
    [Draw.pde, Keyboard_Inputs.pde, Logging.ino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]
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2016-06-11 Change the telemetry to be be done in two seperate streams. for some reason, one really long stream was causing the i2c reads from the MPU to fail.
    [Draw.pde, Logging.ino, MPU_6050_02_ESC_PID.ino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]
2016-06-13 added additional graphing of rate pterm, iterm and dterm. had some good pid values working but then same / very similar pid values started oscillating. iterm help but is problematic if you don't star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
    [Draw.pde, PID_FrontEnd_v03.pde, Serial_Read.pde]
2016-06-23 more pid tuning. I'm calling this good. stable on the single boom. if this doesn't work on the full quad then something else is going on.
    [MPU_6050_02_ESC_PID.ino]
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2016-08-11 added moouseWheel support for throttle and moveMove for setpoint. for some reason I'm getting fifo overflows when submitting commands via the mouse, but no issues when submitting commands via the key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
    [Inputs.ino, Logging.ino, MPU_6050_02_ESC_PID.ino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]
2016-10-03 Back at it again.... fix a few process bugs that must have been there last time. PID settings with cascading PIDs seems to be working ok.
    [ESC.ino, I2C.ino, Inputs.ino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]
2016-10-09 more pid tuning. I have removed the stability check offest from the AC and BD readings.
    [Inputs.ino, MPU.ino, MPU_6050_02_ESC_PID.ino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]
2016-10-17 Added teh ESC libarary, this might be a better choice over the Servo libary. Reverted back to a single pid loop, but I'm not able to get the PIDs to tune at all. found my old checkin notes around the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
    [ESC.ino, Logging.ino, MPU.ino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]
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2016-10-20 Copied the arduino servo libarary to MyServo, updated code to use either the ESC library or the MyServo library. Did some testing with the ESC library and still same tuning issues. Next up is the tes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
    [Config.h, ESC.ino, MPU.ino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]
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2016-10-22 Added an additional esc manual for the Spider ESC being tested. I don't think this are the correct manuals but want to have a copy as I start to track this down.
